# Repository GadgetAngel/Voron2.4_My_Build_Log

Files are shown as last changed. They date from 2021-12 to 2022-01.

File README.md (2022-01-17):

## This is a Build Log for my Voron 2.4 250 mm DIY 3D Printer called "QUEEN":

My Voron 2.4 3D Printer has a name "QUEEN".

This repository contains wiring diagrams, specification sheets, any documentation I use to complete my Voron 2.4 build. I also am including aesthetic designs for QUEEN's back panel and side panels.

# This repository uses LFS extension

```
I use Git for Windows with VScode to manage this repository.  I also use Git LFS extensions for all the files.

Install Git with LFS extensions: https://git-lfs.github.com/

To Download the whole repository do the following: select the "Clone or download button" and
click on "paste to clipboard" button so you can place the URL for the GitHub repository
to the clipboard. Now Open Git Bash.  Change the current working directory to the location
where you want the cloned directory.
Type git clone, and then paste the URL you copied earlier.
$ git clone https://github.com/GadgetAngel/Voron2.4_My_Build_Log.git
Press Enter to create your local clone.
Now open Window explorer to the location of local clone.
```

## This whole repository can be downloaded as one large zip file from my Google Drive at: (if downloading via LFS is giving you are hard time)

## xxxxxxxxxxxxxxxxxxxxxxxxxxxxxxxxxxxxxxxxxxxxx

## Mother board I plan on using:

I will be using the Octopus Pro V1.0 board as the mother board for my Voron 2.4 printer.
I will be powering my TMC5160 PRO stepper motor drivers with 48V DC.

## Planning Phase:

I am ~~still planning~~ done planning my Voron 2.4 build.

I have all my PIF parts and sourced all my parts via "sub-kits".  This will be explained later.

I wanted to post an Excel spreadsheet for sourcing all my "sub-kits" or individual items for my Voron 2.4 ~~, but I need to remove it from a bigger spreadsheet I have been using to keep track of a lot of different information.  After I get done with the electronics case wiring diagram, I will work on providing a~~ [Here is the Excel spreadsheet as a sourcing guide for my Voron 2.4](/QUEEN_Sourcing_BOM).

## MODS I plan for QUEEN:

### Fusion 360 CAD files and STEP files:

I have spent 3 months creating the 3D model of my QUEEN Voron 2.4 250 mm³ build.

I have used the CAD models from each MOD (listed below) and incorporated the respective MOD's CAD model into my QUEEN Fusion 360 model.  After working in Fusion 360 for the past 3 months I have become aware of a couple of things:

1.  When exporting sub-Assemblies from Fusion 360 in .STEP format the only sub-assemblies that get put into the STEP file are the sub-assemblies that are visible at the time the exported STEP file is created.  So when you use STEP files expect all the sub-assemblies to be visible when you first open up the STEP file.  You will have to turn off the options that you do not want to see after you upload the STEP file to Fusion 360 (or your CAD software).

2. If a MOD did not have a Fusion 360 CAD model, I used the .stl files from the MOD and used Fusion 360 to convert the .stl files into parametric bodies.

3.  If you upload .f3d sub-Assembly file and all sub-assembly options are turn on, then please just turn off the sub-assemblies you do not want to see. Sometimes, I exported the .STEP files at the same time I was creating the .f3d files, I might have left options turned on, so I could save the .STEP file.

4. I have noticed that if one uses the "save a copy as ..." option that parts will lose their position (x,y,z).  So to create the sub-assemblies I did a "copy" to the clip board and then placed the clip board contents into a new file and saved that file.

GadgetAngel's Voron 2.4 Fusion 360 CAD model (.f3d) and (.STEP) files:

The full model for QUEEN has a fusion 360 (.f3d) file and STEP file.  The STEP file for the full model has been integrated by myself from all the sub-assemblies STEP files. This way I could check the sub-assembly files to ensure that they were created correctly.

1.  [QUEEN's Voron 2.4 Fusion 360 model and STEP version](./CAD/QUEEN_Voron_2.4_Build_ZIP_files)

2.  [QUEEN's Voron 2.4 Fusion 360 subAssembly model (.f3d) and .STEP versions for the Electronics from the Bottom Electronics Case](./CAD/Electronics_forBottom_Electronic_Case/ZIP_files)

3.  [QUEEN's Voron 2.4 Fusion 360 subAssembly model (.f3d) and .STEP versions for Electronics from the LitterBox Case](./CAD/Electronics_forLitterBox_Case/ZIP_files)

4.  [QUEEN's Voron 2.4 Fusion 360 subAssembly model (.f3d) and .STEP versions for the LEDs](./CAD/LEDs/ZIP_files)

5.  [QUEEN's Voron 2.4 Fusion 360 subAssembly model (.f3d) and .STEP versions for all Panels & Clips](./CAD/Panel_Mounting/QUEENv98_SubAssmbly_Panel&Clips_ZIP_files)

6.  [QUEEN's Voron 2.4 Fusion 360 subAssembly model (.f3d) and .STEP versions for different panels, see this directory for additional sub-assemblies](./CAD/Panel_Mounting)

7. [QUEEN's Voron 2.4 Fusion 360 subAssembly model (.f3d) and .STEP versions for all Skirts](./CAD/Skirts/QUEENv98_SubAssmbly_ALL_Skirts_ZIP_files)

8. [QUEEN's Voron 2.4 Fusion 360 subAssembly model (.f3d) and .STEP versions for different Skirts (i.e., Front Skirt, Left-Side Skirt, etc.), see this directory for additional sub-assemblies](./CAD/Skirts)

9. [QUEEN's Voron 2.4 Fusion 360 subAssembly model (.f3d) and .STEP versions for all the mods located under the Heated Bed & a Filament Runout Sensor](./CAD/Under_Heated_Bed/ZIP_files)

10. [QUEEN's Voron 2.4 Fusion 360 subAssembly model (.f3d) and .STEP versions for my Z Driver Tensioner Mod](./CAD/Z_Drive/ZIP_files)

11. [QUEEN's Voron 2.4 Fusion 360 subAssembly model (.f3d) and .STEP versions for the Exhaust Filter](./CAD/Exhaust_Filter/ZIP_files)

12.  [QUEEN's Voron 2.4 Fusion 360 subAssembly model (.f3d) and .STEP versions for the Frame](./CAD/Frame/ZIP_files)

13. [QUEEN's Voron 2.4 Fusion 360 subAssembly model (.f3d) and .STEP versions for the Gantry](./CAD/Gantry/ZIP_files)

14. [QUEEN's Voron 2.4 Fusion 360 subAssembly model (.f3d) and .STEP versions for the Litter Box Mod and its sub-assemblies, see this directory for additional sub-assemblies](./CAD/Litter_Box_CAD)

15. [QUEEN's Voron 2.4 Fusion 360 subAssembly model (.f3d) and .STEP versions for the Z-Endstop called the "SexBolt Z-Endstop"](./CAD/Z_Endstop/ZIP_files)

16. [QUEEN's Voron 24 Fusion 360 subAssembly model (.f3d) and .STEP version for the BTT piTFT50 V2.0 articulating arm with display mount](./CAD/Skirts/Front/Middle/ZIP_files)

---

### ".STL List" of files needed for each MOD:

I will be publishing a folder of .stl files for all the printed parts I am using for my QUEEN build, including the ones from my PIF parts ~~(coming soon)~~.

My intent is to list the files needed in each Sub-Assembly and indicate which ".stl files" need to be replaced or exchanged for a Modded ".stl" file.  I think an EXCEL spreadsheet would help with this task and can be found [here](/The_.STL_Files/Excel_Spreadsheet_.stl_files).

The ".STL" files for my QUEEN Voron 2.4 build can be found [here](./The_.STL_Files/Copy_of_.STLs_forQUEEN_As_Built_will-not-be-updated)

---

### Voron 2.4 MODS I plan on using for my Build (250 mm³ Build):

Tool head PCB board (MOD) I am using:

1. [Hartk1213's "Voron Afterburner Toolhead Board v3.rabbit (also known as ERCF PCB board)"](https://github.com/VoronDesign/Voron-Hardware/tree/master/Afterburner_Toolhead_PCB).

    * [Buy Hartk1213's ERCF PCB board at deepfriedhero.in website](https://deepfriedhero.in/products/voron-afterburner-toolhead-board-v3-rabbit?_pos=1&_psq=v3.&_ss=e&_v=1.0)

    * [Wiring Diagram for "Voron Afterburner Toolhead Board v3.rabbit"](https://github.com/VoronDesign/Voron-Hardware/blob/master/Afterburner_Toolhead_PCB/Images/Wiring/ERCF-Toolhead%20SKR%201_4%20wiring.png)

    * Also see my [wiring harness diagram!](https://github.com/GadgetAngel/Voron2.4_My_Build_Log/blob/main/Wiring_Harness_Diagram/Voron_2.4_Tool_Head_PCB__Wiring_Harness.jpg)

---

Other MODS I am using for my QUEEN build (Z belts 9 mm; XY belts 6 mm):

1. [Arkeet's "MGN12 Mod"](https://github.com/VoronDesign/VoronUsers/tree/master/printer_mods/arkeet/mgn12);

2. [Hartk1213's "PINS Mod"](https://github.com/hartk1213/MISC/tree/main/Voron%20Mods/Voron%202/2.4/Voron2.4_Pins_Mod);

3. [Ramalama2's "Misumi_RBPB5 Mod"](https://github.com/Ramalama2/Voron-2-Mods/tree/main/Misumi_RBPB5);
[Note: this replaces the GE5C Mod](https://github.com/hartk1213/MISC/tree/main/Voron%20Mods/Voron%202/2.4/Voron2.4_GE5C);

4. [0ndsk4's "Nevermore Micro Filter Mod"](https://github.com/nevermore3d/Nevermore_Micro);

5.  I combined two user mods into one mod for the "Z Drive Motor Tensioner Mod":

    * Z Motor A/B Unit combined from [Edwardyeeks' "V2.4_z_drive_motor_tensioner_mod"](https://github.com/VoronDesign/VoronUsers/tree/master/printer_mods/edwardyeeks/V2.4_z_drive_motor_tensioner_mod); with my modification for the front Skirts for switches and Hour counter;

    * Z Motor A/B Motor Unit combined from [Spaghetti-Bolognese's "Z Driver System Mods"](https://github.com/VoronDesign/VoronUsers/tree/master/printer_mods/Spaghetti-Bolognese/Z_drive_motor_mount);

6. [Jlas1's "Klicky Probe Mod"](https://github.com/jlas1/Klicky-Probe) and information about the Klicky Probe mod from [Ramalama2's "KlickyShare GitHub repo"](https://github.com/Ramalama2/Voron-2-Mods/tree/main/KlickyShare); I also used the following "user mods" for the "Klicky Probe Mod":

    *   ~~[bluedragonx's "BlueDragonX's Klicky Mods" ](using built-in Klicky Probe to X-Axis Carriage Frame): https://github.com/jlas1/Klicky-Probe/tree/main/Printers/Voron/v1.8_v2.4_Legacy_Trident/Usermods/bluedragonx;~~

     Bluedragonx's user mod changes the X-Axis Carriage Frame pieces to allow for a built-in Klicky Probe. I decided to use the regular Klicky Probe mode and a combination of the following two user mods for the Klicky Probe body (this way the Klicky Probe is **not** built into the X-Axis Carriage) and I can decide to use the Euclid Probe, if I so desire [See item #47](#47-derpimus-euclide_probes-omronrotatedxraildock_v2):

    *   [StefanRaatz's Klicky Mods](https://github.com/jlas1/Klicky-Probe/tree/main/Printers/Voron/v1.8_v2.4_Legacy_Trident/Usermods/StefanRaatz); This is a modified Klicky probe with two holes so that you can feed through the uninsulated part of the cable a little more. Gave me better contact.

    *   [Oc_geek's More Robust Klicky Probe Mod](https://github.com/jlas1/Klicky-Probe/tree/main/Printers/Voron/v1.8_v2.4_Legacy_Trident/Usermods/oc_geek); Beefier column and revised holes for zip tie (was def too small); reduced height 1 mm (was excess) Chambered bottom in all direction (also sides) on the probe carriage Microswitch body exposed by a tiny bit.

7. [Whoppingpochard's "Ti Backers Mod"](https://github.com/tanaes/whopping_Voron_mods/tree/main/extrusion_backers); Y backers 30 mm from front; X backer 35 mm from the Y axis drag chain;

8. [Ramalama2's "Front_Idlers mod" ](https://github.com/Ramalama2/Voron-2-Mods/tree/main/Front_Idlers); - these are replacement for Phalanx's "Other-V2-Idlers" mod;

    * Here is the information on Phalanx's "Other-V2-Idlers mod" if you are interested.  [Phalanx's "Other-V2-Idlers mod"](https://github.com/VoronDesign/VoronUsers/tree/a425971f2986578e2e5c10e638f59d02172687c1/printer_mods/Phalanx/Other-V2-Idlers);

~~9. [Badnoob's "AB-BN30 Afterburner mod"](https://github.com/VoronDesign/VoronUsers/blob/master/printer_mods/Badnoob/AB-BN/Readme.md);~~ I will be using the Stealthburner Mod instead. [Please see item #48](#48-voron-design-teams-stealthburner-mod)

####     10.	[Hartk1213's "Sexbolt Z-Endstop Mod"](https://github.com/hartk1213/MISC/tree/main/Voron%20Mods/Voron%202/2.4/Voron2.4_SexBolt_ZEndstop);

11.	Cover for Toolhead, I created my own ([in this repository](https://github.com/GadgetAngel/Voron2.4_My_Build_Log/blob/main/The_.STL_Files/Copy_of_.STLs_forQUEEN_As_Built_will-not-be-updated/Gantry/X_Axis/X_Carriage/Direct_Fee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)) - from [Hartk1213's "ERCF covers for the LGX extruder"](https://github.com/VoronDesign/Voron-Hardware/tree/master/Afterburner_Toolhead_PCB/STLs/LGX); I cut the front of the LGX cover for ERCF cover for Stealthburner. See also [Th3fallen's website for the LGX_PCB_Mount_Heatset.stl file](https://github.com/th3fallen/Voron-Hardware/tree/feature/add-heatset-lgx-pcb-mount/Afterburner_Toolhead_PCB/STLs/LGX);

12.	[Whoppingpochard's "Z_Drive_Belt_Exit_Covers Mod"](https://github.com/tanaes/whopping_Voron_mods/tree/main/Z_belt_cable_cover);

13.	[Edwardyeeks' "Decontaminator_Purge_Bucket_&_Nozzle_Scrubber Mod"](https://github.com/VoronDesign/VoronUsers/tree/master/printer_mods/edwardyeeks/Decontaminator_Purge_Bucket_%26_Nozzle_Scrubber);

14.	[Hernsl's "Bottom_panel_mag_clip Mod"](https://github.com/VoronDesign/VoronUsers/tree/master/printer_mods/hernsl/bottom_panel_mag_clip);

15.	[Wile-e1's "Deck_Panel_Support_Clips Mod"](https://github.com/VoronDesign/VoronUsers/tree/master/printer_mods/wile-e1/Deck_Panel_Support_Clips);

16.	[Tayto-chip's "Skirt_switch_mod"](https://github.com/VoronDesign/VoronUsers/tree/master/printer_mods/tayto-chip/skirt_switch_mod) - with my modifications;

17.	[Leandromarceddu's "PowerSkirt Mod"](https://github.com/VoronDesign/VoronUsers/tree/master/printer_mods/leandromarceddu/PowerSkirt) - with my Modifications;

18.	[StvPtrsn's "Side_Fan_Support_No_Tape Mod"](https://github.com/VoronDesign/VoronUsers/tree/master/printer_mods/StvPtrsn/Side_Fan_Support_No_Tape);

19.	[MarcPot's "Skirt_Mod_250 Mod"](https://github.com/VoronDesign/VoronUsers/tree/master/printer_mods/MarcPot/Skirt_Mods); - with my modification so that you can use this with the magnetic bottom panel;

20. My BTT-PITFT5-Mount Mod come from the following sources:

    * [Alanho's "BTT_PITFT50_v2_Mount Mod"](https://github.com/VoronDesign/VoronUsers/tree/master/printer_mods/alanho/BTT_PITFT50_v2_Mount);

    * [Smaseface's "BTT-PITFT5-Mount mod"](https://github.com/smaseface/BTT-PITFT5-Mount-for-Voron-v2.4);

    * [Revnull's "Articulating arm" from his "rpi_7in_display_mount mod"](https://github.com/VoronDesign/VoronUsers/tree/master/printer_mods/revnull/rpi_7in_display_mount);

    * [driftology's "Fysetc Paneldue 7i V3 Voron 2 Adapter on Thingiverse.com"](https://www.thingiverse.com/thing:4571677);

21.	[Randell's "Microswitch_Endstop POD"](https://github.com/VoronDesign/VoronUsers/tree/master/printer_mods/randell/Microswitch_Endstop);

22. [Ramalama2's "Misumi_Cable_Clip mod"](https://github.com/Ramalama2/Voron-2-Mods/tree/main/Misumi_Cable_Clip);

23. [Ramalama2's "AB_Plug_Microfit mod"](https://github.com/Ramalama2/Voron-2-Mods/tree/main/AB_Plug_Microfit); or [AB_Plug_JST-XHmod](https://github.com/Ramalama2/Voron-2-Mods/tree/main/AB_Plug_JST-XH); or you could also use the Voron Design Team's ["Tie-down the AB motors cables to the Z-Beam Mod"](https://github.com/VoronDesign/Voron-2/blob/Voron2.2/STLs/VORON2.2/Gantry/%5Ba%5D_cable_anchor_x4_rev1.stl);

####       24.  [Ramalama2's "Panel_Clips"; I will use the midspan clips for sides and top](https://github.com/Ramalama2/Voron-2-Mods/tree/main/Panel_Clips); - (use 6 mm version - 3 mm panel and 3 mm of foam tape);

25. [Richardjm's "ADXL345 Mount Mod"](https://github.com/richardjm/VoronUsers/tree/richardjm/adxl-chain/printer_mods/richardjm/adxl-chain); I used information from [Padok's ADXL345 Mount](https://github.com/VoronDesign/VoronUsers/tree/master/printer_mods/padok/chain_anchor-ADXL345_mount);

26. [Eddie's "LED_Bar_Clip mod"](https://github.com/VoronDesign/VoronUsers/tree/master/printer_mods/eddie/LED_Bar_Clip);

27. [Hartk1213's "AB Spinner (Voron2.4_Spinner) mod"](https://github.com/hartk1213/MISC/tree/main/Voron%20Mods/Voron%202/2.4/Voron2.4_Spinner); or [Rubber Ducky Spinner Mod](https://discord.com/channels/460117602945990666/828406858271162378/875463215721644032)

28. [42bios' "corner_panel_clip_cable mod"](https://github.com/VoronDesign/VoronUsers/tree/master/printer_mods/42bios/corner_panel_clip_cable); Also my own modification for these clips so I can use them to mount the Mikro10 Illumination Edge Bracket on the side panels.

29. [OV1A's "WAGO+221+DIN+rail+holder mod" from Thiniverse.com](https://www.thingiverse.com/thing:4972435); Used to mount the WAGO nuts on the DIN rails.

30. [The0bone's "Voron 2.4 China Chain Guide mod" on Prusaprinters.org](https://www.prusaprinters.org/prints/69683-voron-24-china-chain-guide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);

31. For handling the thermal expansion on the Build Plate for QUEEN, I added the Mandala Rose Works's ["Matched Height Kinematic Kit"](https://www.mandalaroseworks.com/shop/voron/matched-height-kinematic-kit) along with ["Voron 250 Standard Bed"](https://www.mandalaroseworks.com/shop/voron/voron-250-standard-bed),

    The following will be needed if you add the kinematic kit to your Voron 2.4 Build:
    *  [Modified Purge Bucket](https://github.com/GadgetAngel/Voron2.4_My_Build_Log/tree/main/The_.STL_Files/GA_modded_STLs/Decontaminator_Purge_Bucket_%26_Nozzle_Scrubber_MOD);
    *  [buy a longer sexbolt for](https://www.amazon.com/gp/product/B07GSQZWNP) [Item #10](#10hartk1213s-sexbolt-z-endstop-mod) and
    *  buy some [Openbuild's Angled brackets](https://deepfriedhero.in/products/openbuilds-angle-corner-connector?_pos=2&_sid=c4c7e2ca4&_ss=r), or you could just use blind joints;

32. [GadgetAngel's "Litter Box mod"](https://github.com/GadgetAngel/Voron2.4_My_Build_Log/tree/main/Electronics_Case_Wiring_Diagram/Litter_Box_Mod);

33. I also used all [Trident DIN clips](https://github.com/VoronDesign/Voron-Trident/tree/main/STLs/ElectronicsBay) for mounting electronics and I used [Trident 3D Printed Parts on the MGN12 Mod](https://github.com/VoronDesign/Voron-Trident/tree/main/STLs/Gantry/X_Axis/X_Carriage). **Thank you, Voron Design Team for all your hard work!**

34. [Nemgrea & Geoffreyyoung's "LGX Extruder Mod to replace the Clockwork extruder"](https://github.com/VoronDesign/VoronUsers/tree/master/printer_mods/geoffreyyoung/lgx);

35. [LoCoCNC's "Wire_grommets"](https://github.com/VoronDesign/VoronUsers/tree/master/printer_mods/LoCoCNC/wire_grommets); modified for Kinematic Bed;

36. [Danowar's "Humidity_Sensor_Bracket"](https://github.com/VoronDesign/VoronUsers/tree/master/legacy_printers/printer_mods/Danowar/Humidity_Sensor_Bracket);

37. [Mikro10 Illumination Edge Bracket for the Side panels](https://www.wired4signsusa.com/products/edge-lit-led-extrusion-for-1-4-acrylic-mikro10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); I modified [42bios' "corner_panel_clip_cable mod"](https://github.com/VoronDesign/VoronUsers/tree/master/printer_mods/42bios/corner_panel_clip_cable) so I could mount the Mikro10 illumination edge bracket to light the side panels.

38. [Boingomw's "Wago_mount mod"](https://github.com/VoronDesign/VoronUsers/tree/master/printer_mods/Boingomw/Wago_mount) used for Wago mount near the Build Plate;

39. [GSL12's "wago_221_mount mod"](https://github.com/VoronDesign/VoronUsers/tree/master/legacy_printers/printer_mods/GSL12/wago_221_mount); Used these to place Wago nuts around the whole Voron 2.4 printer mounted to the extrusions.

40. [Jeoje's "Molex_MLX_Microfit_Bed_Connector_Mount Mod"](https://github.com/VoronDesign/VoronUsers/tree/master/printer_mods/jeoje/Molex_MLX_Microfit_Bed_Connector_Mount);

41. [Richardjm's "Backplate blanking plate mod"](https://github.com/VoronDesign/VoronUsers/tree/master/printer_mods/richardjm/back-plate);

42. [Jeoje's "Z_Chain_Guide_Thermistor_Mount mod"](https://github.com/VoronDesign/VoronUsers/tree/master/printer_mods/jeoje/Z_Chain_Guide_Thermistor_Mount);

43. [BladeScraper-Designs' "Horizontal-Spool-Holder Mod"](https://github.com/VoronDesign/VoronUsers/tree/master/printer_mods/BladeScraper-Designs/Horizontal-Spool-Holder);

44. [Empusas' "BTT_Filament_Motion_Sensor_Mount Mod"](https://github.com/VoronDesign/VoronUsers/tree/master/printer_mods/Empusas/BTT_Filament_Motion_Sensor_Mount);

45. [Ellis' "Bed_Fans Mod"](https://github.com/VoronDesign/VoronUsers/tree/master/printer_mods/Ellis/Bed_Fans);

46. [Ramalama2's "Misumi_Led_Corners"](https://github.com/Ramalama2/Voron-2-Mods/tree/main/Misumi_Led_Corners);

#####     47. [Derpimus' Euclide_Probe's "OmronRotatedXRailDock_v2"](https://discord.com/channels/460117602945990666/916406093339566120/923047248051462226);

#####     48. [Voron Design Team's "Stealthburner Mod"](https://github.com/VoronDesign/Voron-Afterburner/tree/sb-beta/STLs);

49. [Voron Design Team's "Z Rail end stops"](https://github.com/VoronDesign/Voron-2/blob/Voron2.2/STLs/VORON2.2/Gantry/%5Ba%5D_z_rail_stop_x4_rev1.stl);

50. [AlexanderT-Moss's 270-Clamping-Hinges for the front doors](https://github.com/VoronDesign/VoronUsers/tree/master/printer_mods/AlexanderT-Moss/270-Clamping-Hinges) [instead of Item #24's Front door clips](#24--ramalama2s-panel_clips-i-will-use-the-midspan-clips-for-sides-and-top---use-6mm-version---3mm-panel-and-3mm-of-foam-tape);

51. [AlchemyEngine's Skirt-Microfit-Inserts](https://github.com/alchemyEngine/EnragedRabbitProject/tree/main/usermods/Skirt-Microfit-Inserts) - I modified it. So I could [mount a Reset button for the BTT V1.2 Relays](https://github.com/GadgetAngel/Voron2.4_My_Build_Log/blob/main/The_.STL_Files/Copy_of_.STLs_forQUEEN_As_Built_will-not-be-updated/LitterBox_Mod/Electronics/%5Ba%5D_R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) shown on my AC Wiring Diagram;

52. [V6cl's Lift Handles](https://github.com/v6cl/My-Voron2.4-Customs/tree/main/LiftHandle) - I modified the [Lift Handles](https://github.com/GadgetAngel/Voron2.4_My_Build_Log/tree/main/The_.STL_Files/Copy_of_.STLs_forQUEEN_As_Built_will-not-be-updated/Panel_Mounting/LiftHandles_11mm), so they will fit my side panels which have edge lighting.  Instead of 7 mm clearance I will need 11 mm clearance.

53. [V6cl's Panel_Locker](https://github.com/v6cl/My-Voron2.4-Customs/tree/main/Panel_Locker) as the front door handles.

If you are looking for 3D CAD models for the different Voron Build plates you can find them at https://github.com/lecktor/Voron-V2.4

I created a 3D CAD model for the Mandala Rose Works's MIC6 Build plate for the 250 mm build. You can find it at https://github.com/GadgetAngel/Voron2.4_My_Build_Log/tree/main/CAD/Under_Heated_Bed.

## How I Calculated the Power Requirements for my Voron 2.4 Build:

I know a lot of you already know the answer but for the rest of us that are still learning about bipolar stepper motors and stepper drivers I will describe the process I used.  I never realized that the motors I own are **bipolar-series motors**.

To me when things are connected in series the wires are daisy-chained together (positive lead1, negative lead1 is connected to positive lead2, negative lead2).

When things are wired in parallel then the positive leads are connected together and the negative leads are connected together.

So I thought the 3D printer motors where connected together in parallel on the 3D printer, which they are. If you look at the **system in a "macro" view** not a "micro" view.

My problem was not understanding the term "series" and "parallel" when it applies to the internal wiring of the 4-wire bipolar motor (a "micro" view).

I had to look at an 8-wire bipolar motor before I actually got it through my thick head.

Maybe this will help others:

[Drawing of 8 wire bipolar-parallel motor](https://www.google.com/imgres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)

[Drawing of 8 wire bipolar-series motor](https://www.google.com/imgres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)

So ALL my motors are 4-wire bipolar-series motors!

 To Determine the amount of Power Required for your Voron 2.4 build:

 Fact: During a Z Hope move 6 motors will be active at a time.

 Fact: Extruder (E) Motor LDO-42STH20-1004ASH:
		Rated Peak current: 1.0A/ Phase

 Fact: Z motors and AB motors are LD0-42STH40-2004MAH
		Rated Peak current: 2.0A / Phase

 Rule of Thumb (https://robotics.stackexchange.com/a/16333/31219):

 1. Power_supply_current = number_of_motors * 1/3 * motor_peak_current for "bipolar-series motors" (All LDO motors are bipolar-Series Motors!)

 2. Power_supply_current = number_of_motors * 2/3 * motor_peak_current for "bipolar-parallel motors"

 Since ALL LDO motors I own are bipolar-Series Motors we will use Rule of Thumb #1 ONLY!

 Power_ supply_current = (5 * 1/3 * 2.0 Amps) + (1 * 1/3 * 1.0A) = 3.333 + 0.333 = 3.6667 or 4 Amps.

 So for **my bipolar-series motors** I want to know many Watts of power is 4 Amps at 48 VDC?

 Answer: Watts = Volts * Amps

 So, 48VDC * 4 Amp = 192 Watts or 200 Watts PSU (if the PSU supplies the full power without an aluminum plate for heat dissipation [PSU's Derating Curve]).

Options for powering my Voron 2.4 printer at 48 VDC, and 24 VDC (running all HT motors from LDO at 48VDC) with the following:

See UHP-200 Spec Data sheet : https://www.meanwellusa.com/upload/pdf/UHP-200(R)/UHP-200-spec.pdf

See UHP-350 Spec Data sheet : https://www.meanwellusa.com/upload/pdf/UHP-350(R)/UHP-350-spec.pdf

See UHP-500 Spec Data sheet : https://www.meanwellusa.com/upload/pdf/UHP-500(R)/UHP-500-spec.pdf

If you are having a hard time finding UHP-xxx series of power supplies, there are two names for these UHP supplies.  One name is UHP-350-24, UHP-350-48 and so on. While the other name is UHP-350R-24, UHP-350R-48 and so on.  The extra "R" in the model number just indicates that you have the option of wiring 2 power supplies in parallel.  The "R" version will work if you can not find the regular version to buy.

---

1. 48V PSU UHP-200-48 (AC to DC PSU)[(4.2A*0.8)= 3.36 Amps; I need 4 Amps! [without an aluminum plate, so 80%]] : https://www.digikey.com/en/products/detail/mean-well-usa-inc/UHP-200-48/7707242

2. 24V PSU UHP-200-24 (AC to DC PSU)[(8.4A*0.8)= 6.72 Amps ; I want at least 9 Amps! [without an aluminum plate, so 80%]]: https://www.digikey.com/en/products/detail/mean-well-usa-inc/UHP-200-24/7707239

---

3. 48V PSU UHP-350R-48 (AC to DC PSU)[(7.3A*0.70)= 5.32 Amps; I need 4 Amps [without an aluminum plate, so 70%]] : https://www.digikey.com/en/products/detail/mean-well-usa-inc/UHP-350-48/7707258; https://www.newark.com/mean-well/uhp-350r-48/power-supply-ac-dc-48v-7-3a/dp/01AH8032?ost=uhp-350r-48

4. 24 PSU UHP-350R-24 [(14.6A*0.70)= 10.22 Amps; I want at least 9 Amps [without an aluminum plate, so 70%]]: https://www.digikey.com/en/products/detail/mean-well-usa-inc/UHP-350-24/7707254;
https://www.newark.com/mean-well/uhp-350r-24/power-supply-ac-dc-24v-14-6a/dp/01AH8029?ost=uhp-350r-24

---

5. 48V PSU UHP-500-48 (AC to DC PSU)[(10.45*0.7)= 7.315 Amps; I need 4 Amps [without an aluminum plate, so 70%]] : https://www.digikey.com/en/products/detail/mean-well-usa-inc/UHP-500-48/8324039;
https://www.newark.com/mean-well/uhp-500-48/power-supply-ac-dc-48v-10-45a/dp/01AH8038?ost=uhp-500-48

6. 24V PSU UHP-500-24 (AC to DC PSU)[(20.9*0.7) = 14.63 Amps; I want at least 9 Amps [without an aluminum plate, so 70%]]: https://www.digikey.com/en/products/detail/mean-well-usa-inc/UHP-500-24/8324036; https://www.newark.com/mean-well/uhp-500-24/power-supply-ac-dc-24v-20-9a/dp/01AH8036?ost=uhp-500-24

---

So I could use option 3 & 4 **OR** 5 & 6.

Since I plan on LEDs; running a Raspberry Pi 4B with a solid state disk drive (via USB 3.1 interface instead of using a Micro-SD card); and a camera, I want to have enough power to add extras to the Voron Build.

I opted to buy the following:

1.  UHP-500-48 for my 48VDC supply
2.  UHP-500-24 for my 24VDC supply
3.  RS-25-5 for my 5VDC supply
4.   ~~UHP-200-12 for my 12VDC supply~~ Since I switched my LEDs from 12VDC and 24VDC so that all LEDs will be NeoPixels, I need another 5VDC PSU instead of a 12V PSU.  So I decided to by a combo PSU that will supply 5VDC and 12VDC. I purchased a [Meanwell RD-50A](https://github.com/GadgetAngel/Voron2.4_My_Build_Log/blob/main/Resources/MeanWell%20RD-50A%20specs.PDF)

I will use the Octopus Pro to power the stepper motor drivers, heater cartridge, temperature sensors, limit switches, and generate signals on PINs to control stuff, but I do not plan on powering stuff off the Octopus Pro board that is considered optional equipment like LEDs, an endoscope or cameras.  Since my Raspberry Pi (running Klipper) is the brains of this setup, I will be using a solid state drive to act as the disk drive for the Raspberry Pi.  This adds additional current draw and the Raspberry Pi will have its own 5V PSU.

All my LEDs are ~~12VDC or 24VDC~~ NeoPixels which are 5VDC. So that is why I am running a second separate 5VDC PSU and added additional current capability to my 24VDC supply.

I plan on running all TMC5160 (HV) PRO stepper motor drivers for all my motors on QUEEN.
I know this is an overkill but if I want the power it will be there, and I do not want to redo wiring at a later date.

~~Likewise, I am hoping to fit all of my electronics into the electronics case for a 250 mm build.~~ Edited: There is not enough room for all the PSU and all the electronics therefore I developed my own "Litter Box" Mod, so I can keep the AC Power in the bottom electronic's case and use my "Litter Box" for the DC electronic components.

[Click here to get explanation about the "Litter Box" Mod](https://github.com/GadgetAngel/Voron2.4_My_Build_Log/tree/main/Electronics_Case_Wiring_Diagram/Litter_Box_Mod).

1/5/2022: Click [here](https://github.com/GadgetAngel/Voron2.4_My_Build_Log/tree/main/Electronics_Case_Wiring_Diagram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) to see further information about the "Voron 2.4 AC wiring diagram".

Click here see the JPG file for the ["Voron 2.4 AC Electrical Wiring Diagram"](https://github.com/GadgetAngel/Voron2.4_My_Build_Log/tree/main/Electronics_Case_Wiring_Diagram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)

To download the PDF just click on the filename ["Voron_2.4_Electronics_Case_Wiring_Diagram_AC_wiring.pdf"](images/Voron_2.4_Electronics_Case_Wiring_Diagram_AC_wiring.pdf) and hit the download button.

## How did I go about calculating the size of the UPS Battery Backup Units I needed for the QUEEN Build and the Voron 2.4-LDO Build

First off, if you have not heard I bought the Voron 2.4 300 mm³ LDO kit.  I need to build a "close to spec" Voron 2.4 printer so that I can build my dream printer "QUEEN".  This way I will have a work horse printer that I can use to further develop my modifications I am making to the QUEEN build.

Back to the issue at hand.  How did I determine the amount of VAC I would need for each of my Voron 2.4 builds?  Once you decide on the power supply units (PSUs) you will be using for your build, get hold of the data sheets for each of the PSU and look at the specification called "INPUT" "AC Current (typ.)" there should be an amount of amps listed for either 115VAC or 230VAC.  For the USA and corresponding countries that use 120VAC (60Hz) or you will see on the spec sheet of the PSU a listing for "115VAC".  While Europe uses 230VAC (50Hz), you will see on the spec sheet of the PSU a listing for "230VAC".  Take the "INPUT AC Current (typ.)" values for your type of power distribution system and add them all together to get a total "INPUT AC Current (typ.)" value. So for sake of an example, I am in the USA, so I added all my "INPUT AC Current (typ.)" values together for my 4 PSU and got a total "INPUT AC Current (typ.)" = 11.7 amps for the QUEEN build.

Now I was looking at the [APC UPS 1500VA UPS Battery Backup and Surge Protector Unit from Amazon](https://www.amazon.com/gp/product/B06VY6FXMM). It says in the title that is has 1500VA. So I take that number and divide 115VAC into it to give me the total INPUT AC Current (typ) that this UPS Battery Backup unit can handle.  So 1500/115 = 13.0434782 Amps maximum.  I only need 11.7 amps. So take 11.7/13.0434782 to see what % of the total I will be using = 0.89699 or 89.699%. So I have 100%-89.699% of overhead left unused which is equal to 10.30% left unused.  As long as I have at least 10% unused overhead available, I will purchase the unit.

Now let us look at the Voron 2.4 LDO kit. When I add up all the "INPUT AC Current (typ.)" values for that build I get a total of 4 Amps.  I have an extra APC UPS unit here at my home that is called [APC UPS 850VA UPS Battery Backup & Surge Protector](https://www.amazon.com/gp/product/B01HDC21FE). So I take 850/115 = 7.3913 Amps maximum.  I am only using 4 Amps. What is my left unused overhead value? 1-(4/7)*100=42.86%. I feel better with an overhead that large.  I personally would not buy a UPS unit that did not give me at least a 10% unused overhead value.

## How to calculate the Amps required for the BIG RED mushroom button

Added on 1/11/2022:

To calculate the total "INPUT AC Current Draw" from your Voron 2.4 build, look at each of the PSUs you have included in your Voron 2.4.  On the data sheet for the PSUs you will see a specification labeled "INPUT" "AC Current (typ.)" there should be an amount of amps listed for either 115VAC or 230VAC. Take the "INPUT AC Current (typ.)" values for your type of power distribution system and add them all together to get a total "INPUT AC Current (typ.)" value.

So for example, I am in the USA, so I added all my "INPUT AC Current (typ.)" values together for the 115VAC option and my 4 PSUs and draw a total "INPUT AC Current (typ.)" value of 11.7 Amps for the QUEEN build. For the Voron_LDO build by total "INPUT AC Current (typ.)" value is 4 Amps.

I purchased this [BIG RED Mushroom Emergency Button](https://www.amazon.com/gp/product/B07RJMVPJ4) which is rated up to 10 Amps. So, for the Voron_LDO build this [BIG RED Mushroom Emergency Button](https://www.amazon.com/gp/product/B07RJMVPJ4) will work without modification.  I can run both the AC "LINE" and the AC "NEUTRAL" wires from the wall outlet into the "BIG RED" mushroom button and use the two NC contacts to switch those lines (one contact per wire).

But for the QUEEN Build the total "INPUT AC Current (typ.)" value is 11.7 Amps, which is above the rated 10 Amps for this [BIG RED Mushroom Emergency Button](https://www.amazon.com/gp/product/B07RJMVPJ4).  The problem is I could not find a BIG RED Mushroom Emergency Button that is rated for 20 Amps on Amazon.  So this is what I have opted to do.  In the USA, we really do not need to switch the AC "Neutral" wire but switching the AC "Line" wire is what is really needed.  Since this [BIG RED Mushroom Emergency Button](https://www.amazon.com/gp/product/B07RJMVPJ4) has TWO normally closed (NC) contacts and each contact is rated for 10 Amps, I can just run the AC "Line" wire into the two NC contacts in parallel. Think of the BIG RED Mushroom button as a DPST switch.  By wiring the contacts up in parallel then each contact will handle 10 Amps and now my BIG RED Mushroom Button can handle 20 Amps on the AC "Line" wire. On the output of the NC contacts the two AC "Line" wires are brought back together for a single output feed.

~~So now I need to change my "AC wiring diagram" to reflect this change in the BIG RED button for the QUEEN Build.~~
I have updated the ["AC wiring diagram"](https://github.com/GadgetAngel/Voron2.4_My_Build_Log/blob/main/images/Voron_2.4_Electronics_Case_Wiring_Diagram_AC_wiring.pdf) to reflect the changes to the BIG RED mushroom Emergency Button.  

I also modified the [Skirt-Microfit-Inserts Mod from Ette's ERCF project](/The_.STL_Files/GA_modded_STLs/Skirt/Front/A/%5Ba%5D_Button_mount%20Z-tensioner_Mod_Front_OR_Rear_Hour_Counter_Skirt_A_300_x2.stl) so that I would have a place to mount QUEEN's "Reset Printer Only"
buttons.  The other four switches will control four Neopixel LED Strings, and they will be on the "DC wiring diagram". I also need to print the 300 mm front skirt version so that I have a place to mount this "Skirt_Insert" called "\[a\]_Button_mount Z-tensioner_Mod_Front_OR_Rear_Hour_Counter_Skirt_A_300.stl" and "\[a\]_Button_mount_Front_OR_Rear_Rocker-switches_Skirt_B_300.stl".

To learn more about parallel circuits see [UNDERSTANDING & CALCULATING PARALLEL CIRCUITS - EXPLANATION](https://www.swtc.edu/Ag_Power/electrical/lecture/parallel_circuits.htm)

Here is a diagram on how to wire two NC contacts up in parallel:

ParallelDiagram

## The PDF file of the "Color PIN Diagram" for the Octopus Pro V1.0:

You can view the PDF in your browser by clicking on the filename ["BIGTREETECH-Octopus-Pro-V1.0-Color-PIN-V3.0.pdf"](https://github.com/GadgetAngel/BTT_Octopus_Color_PIN_Diagram/blob/main/BTT_Octopus_Pro_V1.0_Color_PIN_Diagram/BIGTREETECH-Octopus-Pro-V1.0-Color-PIN-V3.0.pdf) and then hit the download button.

You can view an even higher resolution image (give it a minute or two to load, it takes longer due to the higher resolution) when you view the PDF in your browser by clicking on the filename ["BIGTREETECH-Octopus-Pro-V1.0-Color-PIN-V3.0-400ppi.pdf"](https://github.com/GadgetAngel/BTT_Octopus_Color_PIN_Diagram/blob/main/BTT_Octopus_Pro_V1.0_Color_PIN_Diagram/BIGTREETECH-Octopus-Pro-V1.0-Color-PIN-V3.0-400ppi.pdf) and then hit the download button.

## A Picture of the "Color PIN Diagram" for the Octopus Pro V1.0:

You can download the JPG file for this "Color PIN Diagram" by clicking on the filename ["BIGTREETECH-Octopus-Pro-V1.0-color-PIN-V3.0.jpg"](https://github.com/GadgetAngel/BTT_Octopus_Color_PIN_Diagram/blob/main/BTT_Octopus_Pro_V1.0_Color_PIN_Diagram/BIGTREETECH-Octopus-Pro-V1.0-color-PIN-V3.0.jpg) or ["BIGTREETECH-Octopus-Pro-V1.0-color-PIN-V3.0-400ppi.jpg"](https://github.com/GadgetAngel/BTT_Octopus_Color_PIN_Diagram/blob/main/BTT_Octopus_Pro_V1.0_Color_PIN_Diagram/BIGTREETECH-Octopus-Pro-V1.0-color-PIN-V3.0-400ppi.jpg) and then hit the download button.

Again, to download the PDF just click on the filename ["BIGTREETECH-Octopus-Pro-V1.0-Color-PIN-V3.0.pdf"](https://github.com/GadgetAngel/BTT_Octopus_Color_PIN_Diagram/blob/main/BTT_Octopus_Pro_V1.0_Color_PIN_Diagram/BIGTREETECH-Octopus-Pro-V1.0-Color-PIN-V3.0.pdf) or ["BIGTREETECH-Octopus-Pro-V1.0-Color-PIN-V3.0-400ppi.pdf"](https://github.com/GadgetAngel/BTT_Octopus_Color_PIN_Diagram/blob/main/BTT_Octopus_Pro_V1.0_Color_PIN_Diagram/BIGTREETECH-Octopus-Pro-V1.0-Color-PIN-V3.0-400ppi.pdf) and hit the download button.

JPG of Color PIN Diagram

## "Wiring_Harness_Diagram" for QUEEN:

This is the wiring harness diagram I developed for my Voron 2.4 build, it is also in the directory called "Wiring_Harness_Diagram".

Please take notice of the "Notes" section on the "Wiring_Harness_Diagram".

To ensure you see it, I am going to repeat it here:

```
Note about the Hartk1213 v3.rabbit board:
If the jumper pads on the back of the v3.rabbit are configured
incorrectly you could end up damaging your Octopus Pro mother board!!

Because there are two different versions of this Toolhead board around (let’s call them version #1,
and version #2), before powering on your printer, please ensure that the jumper pads on the back of
the v3.rabbit Toolhead board are properly configure for your FANS and ABL!

How to tell which version of the v3.rabbit Toolhead board you own:

If you turn the board over on its back, you will see a bank of jumper pads.  For version #1 of the
v3.rabbit Toolhead board has 4 columns by 3 rows of jumper pads.  For version #2 of v3.rabbit
Toolhead board has 3 columns by 3 rows of jumper pads.  If you have version #1 of the v3.rabbit
Toolhead board (4 columns by 3 rows of jumper pads) than you are responsible for bridging the
jumper pads to your desired voltage (in my case I would solder a bridge to 24VDC for ABL, PCF, HEF,
and FS).  If you have version #2 of the v3.rabbit Toolhead board (3 columns by 3 rows of jumper
pads) than all the selectable voltages default to 24VDC!

Here is what the labels mean:
ABL means auto bed leveling or an inductive probe or the proximity sensor connector;  PCF means
Part Cooling Fan; HEF means Hotend Fan; and FS means Filament Switch Sensor.

For version #1 of the v3.rabbit board, the columns are labeled from left to right: ABL, PCF, HEF,
FS. For version #2 of the v3.rabbit board, the columns are labeled from left to right: ABL, PCF,
HEF.

For version #1 and version #2 the rows are: 1st row is 24VDC; 2nd row is (ABL, PCF, or HEF, {only
on Version #1 FS}); and 3rd row is 5VDC.

If you have version #2 and you want 5VDC, you are going to cut the trace to the 24VDC on the
desired PIN (ABL, PCF or HEF)!
```

JPG of wiring harness Diagram

You can download the JPG file for this "Wiring_Harness_Diagram" by clicking on the filename ["Voron_2.4_Tool_Head_PCB__Wiring_Harness.jpg"](https://github.com/GadgetAngel/Voron2.4_My_Build_Log/blob/main/Wiring_Harness_Diagram/Voron_2.4_Tool_Head_PCB__Wiring_Harness.jpg).

 You can view an even higher resolution image (give it a minute or two to load, it takes longer due to the higher resolution) when you view the JPG in your browser by clicking on the filename ["Voron_2.4_Tool_Head_PCB__Wiring_Harness_400ppi.jpg"](https://github.com/GadgetAngel/Voron2.4_My_Build_Log/blob/main/Wiring_Harness_Diagram/Voron_2.4_Tool_Head_PCB__Wiring_Harness_400ppi.jpg) and then hit the download button.

## PDF version of the Wiring_Harness_Diagram":

You can view the PDF in your browser by clicking on the filename ["Voron_2.4_Tool_Head_PCB__Wiring_Harness.pdf"](https://github.com/GadgetAngel/Voron2.4_My_Build_Log/blob/main/Wiring_Harness_Diagram/Voron_2.4_Tool_Head_PCB__Wiring_Harness.pdf) and then hit the download button.

You can view an even higher resolution image (give it a minute or two to load, it takes longer due to the higher resolution) when you view the PDF in your browser by clicking on the filename ["Voron_2.4_Tool_Head_PCB__Wiring_Harness_400ppi.pdf"](https://github.com/GadgetAngel/Voron2.4_My_Build_Log/blob/main/Wiring_Harness_Diagram/Voron_2.4_Tool_Head_PCB__Wiring_Harness_400ppi.pdf) and then hit the download button.

## "Electronics_Case_Wiring_Diagram" directory you will find the wiring diagram for the electronics case for QUEEN:

Click here see the JPG file for the ["Voron 2.4 AC Electrical Wiring Diagram"](https://github.com/GadgetAngel/Voron2.4_My_Build_Log/tree/main/Electronics_Case_Wiring_Diagram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)

To download the PDF just click on the filename ["Voron_2.4_Electronics_Case_Wiring_Diagram_AC_wiring.pdf"](images/Voron_2.4_Electronics_Case_Wiring_Diagram_AC_wiring.pdf) and hit the download button.

## How Well Will Your Motors Perform on a Voron Build?

You need to look at the torque curve for your motors and see how your motors perform at different voltages.

Here is an Excel spreadsheet that can help you: https://github.com/eddietheengineer/documentation/tree/master/stepper_motor/data

To download the spreadsheet, just click on the file named ["motor_torque_sim_v7_database.xlsm"](https://github.com/eddietheengineer/documentation/blob/master/stepper_motor/data/motor_torque_sim_v7_database.xlsm) and hit the download button.

Once the Excel spreadsheet "motor_torque_sim_v7_database.xlsm" has downloaded, open it up in Excel but remember to "Enable" editing. If you do not enable editing you will not be able to see the "torque curve" graph. Also, the motors that are graphed can be chosen from a dropdown list. The voltage you run the stepper motors at can also be entered as can the current level.

Here are examples of Torque Curves produced by the Excel Spreadsheet:

As you will see when you go from 24V to 48V you can move faster. Also notice that when you go from 48V to 60V the gain is smaller than the jump from 24V to 48V!

Here is the Torque Curve for the specified stepper motors at 24 VDC:

Motor Torque Curve for 24V

Here is the Torque Curve for the same specified stepper motors at 48 VDC:

Motor Torque Curve for 48V

Here is the Torque Curve for the same specified stepper motors at 60 VDC:

Motor Torque Curve for 60V

As you can see when you go from 24V to 48V you can move faster. Also notice that when you go from 48V to 60V the gain is smaller than the jump from 24V to 48V!

## The Original BIGTREETECH Wiring Diagram for the Octopus Pro V1.0:

Original Wiring Diagram

## BIGTREETECH has a GitHub repository for the Octopus Pro V1.0:

The BIGTREETECH GitHub repository for Octopus Pro is located at https://github.com/bigtreetech/BIGTREETECH-OCTOPUS-Pro

## BIGTREETECH has a GitHub repository for the Octopus V1.0/1.1 Board:

The BIGTREETECH GitHub repository for Octopus 1.0/1.1 is located at https://github.com/bigtreetech/BIGTREETECH-OCTOPUS-V1.0

This repository also has information on how to wire up an Octopus V1.0/V1.1 board for a Voron Build and is located at https://github.com/bigtreetech/BIGTREETECH-OCTOPUS-V1.0/tree/master/Octopus%20works%20on%20Voron%20v2.4/Firmware

## How to set up Klipper on a Raspberry Pi

I am using a [Raspberry Pi 4B that I bought from CanaKit](https://www.canakit.com/raspberry-pi-4-extreme-aluminum-case-kit.html). You can choose to run the Raspberry Pi 4B with a micro-SD card, or you can use a solid state drive as your disk drive.

I bought a [Samsung 870 EVO 500 GB SATA (2.5") Solid State Drive (SSD) (MZ-77E500) from Amazon](https://www.amazon.com/gp/product/B08T1QQZ1T) with a [StarTech.com USB 3.1 to 2.5" SATA Hard Drive Adapter](https://www.amazon.com/gp/product/B00XLAZODE).

It does not matter which item you use to boot the Raspberry Pi 4B, but you do need at least a micro-SD card.

The first thing you will need to do is to format the micro-SD card or the SSD.  I have a Windows 10 machine so all my instructions will assume you are using a Windows 10 OS.

Before you can format a SSD you first need to initialize the media. On Window 10, "Right-click" on the startup menu in the lower left corner of your desktop. Choose the "Disk Management" option.  The "Disk Management" tool will automatically ask you if you want to initialize the new disk drive.  Say "Yes". When Windows is done, exit the "Disk Management" Tool. Now you need to create a primary partition for the SSD. Since we will be creating a primary partition of FAT32 larger than 32 GB, we can not use the Windows 10 "Disk Management" Tool to do this.

I like to use the program ["MiniTool Partion Wizard", so click here](https://www.partitionwizard.com/free-partition-manager.html). As a home user you can download it and use it for free. Download and Install the software onto your computer. With the "MiniTool Partion Wizard" you will need to create a primary partion by choosing the square labeled "Disk & Partition Management". Choose the new destination drive and select "Create a partition". Set "Create As" field to "Primary", set "File System" as "FAT32" and accept default for everything else. Select "Ok". Now all that did was place the command into the Que.  You need to select "Apply" to get the software to actually execute the command. Once "MiniTool Partion Wizard" is done creating the primary partion you can format the SSD by choosing the "Format Partition" and set the "File System" field to "FAT32". Leave all other fields at the default. Select "OK" and "Apply". When "MiniTool Partion Wizard" is finished you can exit the software by closing out the window.

For a micro-SD card, all you need to do is place the micro-SD card into an adapter that will allow your Windows 10 machine to read the micro-SD card. I need a micro-SD card to USB reader.  You can use windows to format the micro-SD card by opening Windows file explorer [Win Key]+[E key] select "This PC" now right-click on the micro-SD card and choose "Format". Set the "File System" field to "FAT32" and click "Start".

Once the micro-SD card (or SSD drive) is formatted for FAT32 you are ready to burn the image of "Raspberry Pi OS lite" onto the media. First you need to download the image of [Raspberry Pi OS Lite, by clicking here](https://www.raspberrypi.com/software/operating-systems/). Select "Download" next to the item listed as "Raspberry Pi OS Lite" and save the file onto your local disk drive. Remember where you put it because you will need to navigate to the image file in the next step. Before moving onto the next step take the time now to Un-Zip the folder, so you will be able to access the image (*.img) file.

Once the download is complete, you will need another program called ["Balena Etcher", so click here](https://www.balena.io/etcher/). Select "Download for Windows (x86|x64)" and save the file to your disk drive. Install the "Balena Etcher" software on to your computer.

Open Etcher and choose "Select Image". You now have to navigate to the directory of where you stored the image of "Raspberry Pi OS Lite. The name of the file for my "Raspberry Pi OS Lite" was "2021-10-30-raspios-bullseye-armhf-lite.img". Now choose "Select Drive". Since you formatted the micro-SD card (or the SSD) the media should have been assigned a disk drive letter. Ensure you have selected the correct drive letter.  You do not want to overwrite the wrong drive letter.  Disclaimer: I will not be held responsible for anyone who overwrites their main disk drive for their computer system.  Double check that you selected the correct drive letter and that it matches the one for your micro-SD card (or the SSD) that you will be using with your Raspberry Pi 4B. Once you are sure you have selected the correct drive letter, now select "Flash!". Etcher might give you a warning especially if you are flashing to a SSD, just again ensure you have the correct drive letter and when you are sure tell Etcher "yes or proceed".  Etcher will then take the *.img file and write it to the media. After Etcher is finished it will automatically dismount the media from your computer.  So unplug the USB connector of the micro-SD card (or SSD) and plug it back into your USB port.

We now have to add a file to the micro-SD card (or SSD).  This file is an empty file.  You just need to create the filename "SSH".  I usually just right-click inside the Window Explorer folder for the micro-SD card (or SSD) and choose the option of "New" → "Text document". I assign the name "SSH" and remove the extension ".txt".  This is a very important step the file CAN NOT have a file extension.  The file must be named "SSH" or "ssh" without an extension.  The empty ssh file will tell the "Raspberry Pi OS Lite" operating system to enable the SSH sever automatically upon first boot up.

Once you have added the ssh file to the contents of the micro-SD card (or SSD) it is now time to dismount the media from your computer and plug the media into the Raspberry Pi 4B, so it can boot up (of course you need to ensure you also connect a power supply to the Raspberry Pi 4B and an Ethernet cable).  Once you have plugged in the micro-SD card (or SSD) to the Raspberry Pi, and connect an Ethernet cable to the Ethernet port, turn on the power supply and allow it to boot.

The Raspberry Pi OS will look to see if a micro-SD card is present, if a micro-SD card is present it will try to boot off the micro-SD card. But if a micro-SD card is not present, it will start to look for another media to boot from and this is when it will find the solid state drive.  So for those of you that want to use the SSD as the main boot device make sure that the micro-SD card reader of your Raspberry Pi is empty when you have the SSD attached to the USB 3.0 port.

The Raspberry Pi will boot and then be assigned an IP address on your network.  We need to know the IP address, so we can remotely log in to the Raspberry Pi.  On a Windows 10 machine open up a command prompt window, and type the command "ping raspberrypi.local -4".  Since this is a fresh installation of the Raspberry Pi, all Raspberry Pi are assigned a hostname of raspberrypi after the initial boot.  The default login information is username is "pi" and password is "raspberry". After you perform the windows cmd "ping raspberrypi.local -4", the ping command will display an IP address that it transmitted packets too. Write down the IP address that received those packets.  This is the IP address of your new Raspberry Pi.

To set up Klipper on the new Raspberry Pi you will need to remotely log in into the Raspberry Pi via ssh.  To do this you need another software package called ["Putty", click here](https://www.putty.org/). Install the software on your computer. Now run Putty and enter the IP address (in the Host Name field) you saw in the "ping raspberrypi.local -4" command. Leave the Port number set to 22. Now hit "Open". You should see a window that pops up that says something about the authorization key has not been stored. Just say you trust the device. You will then get the login prompt. Enter in "pi" for the username and "raspberry" for the password.

If you get the "connect rejected" message, then there is something wrong with the ssh server. When you placed the empty ssh file in the file folder of the boot media you either misspelled the filename or left the ".txt" extension on the filename.  You can fix the "connect rejected" message by powering off the Raspberry Pi; removing the boot media from the Raspberry Pi; reattach the boot media to your computer and double-check the empty ssh filename is "ssh" only; then reattach the boot media to the Raspberry Pi and reboot again.

Now you should be logged in to the Raspberry Pi. When you see a "$" this means you need to type a command at the command prompt.  If you see a ">" this means you type a number at the current command prompt. Follow the below sequence to install KIAUH, Klipper, MoonRacker, Mainsail, KlipperScreen and Octoprint.  Once that is all installed we will then be hooking up the Octopus or Octopus Pro boards so that we can flash a new bootloader on to the boards. This new bootloader will allow the Raspberry Pi to talk to the Octopus board.  But for now just follow the below sequence to install everything you will need on the Raspberry Pi 4B. Also, make sure you have an Ethernet cable attached to the Raspberry Pi's Ethernet port:

```
$sudo raspi-config

The raspi-config Menu will be displayed.

>System Options -> change the system password (make note of the password so you do not forget it)
>System Options -> Boot/Autologin -> Console Autologin; turn this on
>System Option -> Network at Boot; turn this on
>Interface Options -> turn on camera interface
>Interface Options -> turn on SSH
>Localization Options -> set Time Zone for your area -> for me USA: Eastern Time
>Localization Options -> set Localization -> if in USA use "en_US.UTF-8"
>Localization Options -> WLAN Country -> set this to your country -> for me USA
>Advanced Options -> expand filesystem
>Finish

$sudo reboot

Now wait for the device to reboot and use Putty to log back into the Raspberry pi and continue onto the next step

$sudo apt update
$sudo apt full-upgrade
$sudo apt autoremove
sudo apt-get install git -y
$cd ~
$git clone https://github.com/th33xitus/kiauh.git
$./kiauh/kiauh.sh

The KIAUH menu will appear.

>1
>1
>2

make a note of the Moonracker Instance (write down the IP address)

>3

make a note of the MJPG-Streamer webcam URLs

>5
>7

make a note of the Octoprint IP address

>B
>Q

```
Now that Klipper and its corresponding software has been installed onto the Raspberry Pi, I want to do a clean reboot before we go onto the next step of compiling the Klipper firmware and updating the mother board (Octopus or Octopus Pro board).

```
$sudo reboot
```

If you have either an Octopus V1.0/V1.1 board or the Octopus PRO board you will need a fresh micro-SD card so that you can transfer the compiled firmware over to the Octopus V1.0/V1.1 board or the Octopus PRO board. You will need to download and install on your PC the software ["winscp", by clicking here](https://winscp.net/eng/download.php). 

The Winscp software will allow you to transfer a file off the Raspberry Pi to your PC's disk drive. This way when the Raspberry Pi has finished compiling the firmware for the Octopus board you can grab the "Klipper.bin" file and transfer it to your PC disk drive and then copy it over to the Micro-SD card that you will place into the Octopus board's Micro-SD card reader.  When you copy the "klipper.bin" file over to the Micro-SD card remember to rename it to "firmware.bin". If the file is not renamed "firmware.bin" then the Octopus boards (V1.0/V1.1 or PRO) bootloader will not be updated properly.

Now we need to apply power to the Octopus board.  I typically power the Octopus board using the USB-C cable when I do this next step (ensure you have the Jumper on the for PWR SELECTION header so that the USB-C can power the 5V rail of the Octopus board)

But you could power the Octopus board by using an independent PSU and attach the 12VDC and GND to the screw terminals (just ensure you **remove** the Jumper from the PWR SELECTION header so that the 5V rail is **not** getting power via the USB-C cable)

Now use the USB-C cable that came with the Octopus board and attach it to the Raspberry Pi (USB 2.0) port.  If the Jumper is on the PWR SELECTION header than the Raspberry Pi will supply the 5VDC to the 5V rail of the Octopus Board and also communicate to the Octopus board via USB. If the Jumper is removed from the PWR SELECTION header than the USB-C cable will be used for communications only.

When the Raspberry Pi reboots, use Putty to log back into the device.

If you have an Octopus V1.0/V1.1 board follow the steps below (skip these steps if you have an Octopus Pro board with the F446 chip or the F429 chip):

```
$./kiauh/kiauh.sh

The KIAUH menu will appear.

>4
>3

[*] Enable extra low-level configuration options by moving the cursor and hitting the space bar until the "*" appears.

The space bar is a toggle so when the "*" appears it means you have selected the item.
When the  "*" is not present it means the item is NOT selected. You use the arrow keys on your keyboard to move up and down the menu.

set Micro-controller Architecture to (STMicroelectronics STM32)
set Processor model to (STM32F446)
set Bootloader offset to (32KiB bootloader)
set Clock Reference to (12 Mhz crystal)
set Communication interface to (USB (on PA11/PA12))
>Q Y

The firmware will compile.

>B
>Q

You will now have to use a micro-SD card to flash the Octopus board with the new firmware. The Octopus board will not 
update the firmware via USB cable! After you have copied the out\Klipper.bin file over to your PC (using Winscp) and onto 
the micro-SD card, please rename the "klipper.bin" file to "firmware.bin".  Once you place the micro-SD card into the 
Octopus board's Micro-SD card reader it will update its bootloader. To ensure that the board really did update the 
bootloader pull the micro-SD card out of the Octopus board and reload it onto your PC. Check to see if the filename has 
been change from "firmware.bin" to "FIRMWARE.CUR".  If the filename changed then the Octopus board updated its bootloader correctly.

```

If you have an Octopus V1.0/V1.1 board or the Octopus Pro board with the F429 chip, skip the following steps.  These steps are for the Octopus PRO board with the F446 chip. If you have an Octopus Pro board that uses the F446 chip, please follow the next steps:

```
$./kiauh/kiauh.sh

The KIAUH menu will appear.

>4
>3

[*] Enable extra low-level configuration options by moving the cursor and hitting the space bar until the "*" appears.

The space bar is a toggle so when the "*" appears it means you have selected the item
when the  "*" is not present it means the item is NOT selected. You use the arrow keys on your keyboard to move up and down the menu.

set Micro-controller Architecture to (STMicroelectronics STM32)
set Processor model to (STM32F446)
set Bootloader offset to (32KiB bootloader)
set Clock Reference to (12 Mhz crystal)
set Communication interface to (USB (on PA11/PA12))
>Q Y

The firmware will compile.

>B
>Q

You will now have to use a micro-SD card to flash the Octopus board with the new firmware. The Octopus board will not 
update the firmware via USB cable! After you have copied the out\Klipper.bin file over to your PC (using Winscp) and onto 
the micro-SD card, please rename the "klipper.bin" file to "firmware.bin".  Once you place the micro-SD card into the 
Octopus board's Micro-SD card reader it will update its bootloader. To ensure that the board really did update the 
bootloader pull the micro-SD card out of the Octopus board and reload it onto your PC. Check to see if the filename has 
been change from "firmware.bin" to "FIRMWARE.CUR".  If the filename changed then the Octopus board updated its bootloader correctly.
```

If you have an Octopus V1.0/V1.1 board or an Octopus Pro board with F446 chip, skip the following steps. These steps are for the Octopus PRO board with the F429. If you have an Octopus Pro board that uses the F429 chip, please follow the next steps:

```
$./kiauh/kiauh.sh

The KIAUH menu will appear.

>4
>3

[*] Enable extra low-level configuration options by moving the cursor and hitting the space bar until the "*" appears.

The space bar is a toggle so when the "*" appears it means you have selected the item
when the  "*" is not present it means the item is NOT selected. You use the arrow keys on your keyboard to move up and down the menu.

set Micro-controller Architecture to (STMicroelectronics STM32)
set Processor model to (STM32F429)
set Bootloader offset to (32KiB bootloader)
set Clock Reference to (8 Mhz crystal)
set Communication interface to (USB (on PA11/PA12))
>Q Y

The firmware will compile.

>B
>Q

You will now have to use a micro-SD card to flash the Octopus board with the new firmware. The Octopus board will not 
update the firmware via USB cable! After you have copied the out\Klipper.bin file over to your PC (using Winscp) and onto 
the micro-SD card, please rename the "klipper.bin" file to "firmware.bin".  Once you place the micro-SD card into the 
Octopus board's Micro-SD card reader it will update its bootloader. To ensure that the board really did update the 
bootloader pull the micro-SD card out of the Octopus board and reload it onto your PC. Check to see if the filename has 
been change from "firmware.bin" to "FIRMWARE.CUR".  If the filename changed then the Octopus board updated its bootloader correctly.

```

### Finding the MCU ID:

At this point if you have an Octopus V1.0/V1.1 or an Octopus Pro with F446 chip or an Octopus Pro with F429 Chip, you have successfully updated its bootloader because the "firmware.bin" filename on the micro-SD card was renamed to "FIRMWARE.CUR"

But we will be needing the MCU ID for out Klipper configuration file, so let's log back into the Raspberry Pi by using Putty.

Now power the Octopus board via which USB-C or with an independent power supply. Connect the USB-C cable from the Octopus board to the Raspberry Pi's USB 2.0 port. We need to find the ID for this connection.

Please do the following:

```
$./kiauh/kiauh.sh

The KIAUH menu will appear.

>4
>6
>1

the menu will refresh, but, **above the menu** you will see something similar to my output (each Octopus board will generate a unique id).

● (USB) MCU #1: /dev/serial/by-id/usb-Klipper_stm32f446xx_3B001B00115053424E363620-if00

Copy this string down because you will have to add it to your Klipper config file later.

>B
>Q
```

If you loose the MCU ID you can always rerun KIAUH option 4, option 6, choose 1 for USB, and it will display the information for you again.

## Klipper firmware supports the Octopus Pro V1.0 board:

Here is the link to the config file on GitHub for the Octopus pro V1.0 board https://github.com/Klipper3d/klipper/blob/master/config/generic-bigtreetech-octopus.cfg.

Here is the link to the Klipper configuration file for the Voron 2.4 printer on the Voron 2.4 GitHub site https://github.com/VoronDesign/Voron-2/blob/Voron2.4/firmware/klipper_configurations/Octopus/Voron2_Octopus_Config.cfg

If you are using the "PROBE" connector for a proximity sensor you will need to add a [probe] section to the "generic-bigtreetech-octopus.cfg" file and ensure that the sensor_pin: PC5

There is only two PINs that are different between the Octopus V1.1 pin-out and the Octopus Pro V1.0 pin-out. The Octopus V1.1 pin-out has PC5 on the EXP2 connector but on the Octopus Pro V1.0 this pin on the EXP2 connector is now "Not Connected (NC)".

The second PIN difference is that on the Octopus V1.1 pin-out PB7 is the signal PIN used on the PROBE/SENSOR connector and on the BLTouch header but on the Octopus Pro V1.0 the signal pin on the PROBE connector is PC5.  Which means that on the Octopus V1.1 board you can only use either a BLTouch or a Proximity Sensor but NOT both. On the Octopus Pro V1.0 since the signal pins for the PROBE connector is different from the BLTouch, if you wanted to, you could use both ports.

If you plan to use a voltage higher than 24V on MOTOR_POWER_IN then please pay attention to the footnote #1 on the "Color PIN Diagram".

You may need to change the Fuse on the MB_POWER_IN. To calculate the maximum amps you will be using on the MB_POWER_IN connection you will need to know the maximum amps allowed on the 24VDC rail for the motherboard.

To calculate the maximum amps allowed on the 24VDC rail on mother board:

 (the four heaters {HE0-HE3}, 3.3VDC rail, 5VDC rail, and 12VDC rail are all produced from the 24VDC rail).

 The maximum amps for 3.3VDC rail is 1 Amp.

 The maximum amps for the 5VDC rail is 8 Amps.

 The maximum amps for 12VDC rail is 4 Amps.

 So the total maximum amps for 3.3VDC rail + 5VDC rail + 12VDC rail is equal to 13 Amps, but the amps needed to run the four heaters needs to be added to this value.

 Since BIGTREETECH supplies us with a 20 Amp fuse, then BIGTREETECH is saying that you have 7 more Amps available for all four heater ports or 1.75 Amps / heater cartridge. Just do not use more than 7 Amps on any combination of the four heater {HE0-HE3} ports!

Please use the "Color PIN Diagram" in [BTT_Octopus_Pro_V1.0_Color_PIN_Diagram](https://github.com/GadgetAngel/BTT_Octopus_Color_PIN_Diagram/tree/main/BTT_Octopus_Pro_V1.0_Color_PIN_Diagram) to obtain the correct PIN assignments.

If you decide to flash a new bootloader to the Octopus Pro V1.0 board (you should not need to because you can upload the new Klipper firmware using the micro-SD card reader) and find that the micro-SD card bootloader no longer works you will want to return the board to its shipment state by finding the original bootloader and "bootloader+firmware" files at https://github.com/GadgetAngel/BTT_SKR_13_14_14T_SD-DFU-Bootloader/tree/main/bootloader_bin/backed_up_original_bootloaders

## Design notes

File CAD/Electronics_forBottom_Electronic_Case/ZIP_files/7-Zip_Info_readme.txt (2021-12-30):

7-Zip 21.07
-----------

7-Zip is a file archiver for Windows.

7-Zip Copyright (C) 1999-2021 Igor Pavlov.

The main features of 7-Zip: 

  - High compression ratio in the new 7z format
  - Supported formats:
     - Packing / unpacking: 7z, XZ, BZIP2, GZIP, TAR, ZIP and WIM.
     - Unpacking only: AR, ARJ, Base64, CAB, CHM, CPIO, CramFS, DMG, EXT, FAT, GPT, HFS,
                       IHEX, ISO, LZH, LZMA, MBR, MSI, NSIS, NTFS, QCOW2, RAR, 
                       RPM, SquashFS, UDF, UEFI, VDI, VHD, VHDX, VMDK, XAR and Z.
  - Fast compression and decompression
  - Self-extracting capability for 7z format
  - Strong AES-256 encryption in 7z and ZIP formats
  - Integration with Windows Shell
  - Powerful File Manager
  - Powerful command line version
  - Localizations for 90 languages

7-Zip is free software distributed under the GNU LGPL (except for unRar code).
Read License.txt for more information about license.

  This distribution package contains the following files:

  7zFM.exe      - 7-Zip File Manager
  7-zip.dll     - Plugin for Windows Shell
  7-zip32.dll   - Plugin for Windows Shell (32-bit plugin for 64-bit system) 
  7zg.exe       - GUI module
  7z.exe        - Command line version
  7z.dll        - 7-Zip engine module
  7z.sfx        - SFX module (Windows version)
  7zCon.sfx     - SFX module (Console version)

  License.txt   - License information
  readme.txt    - This file
  History.txt   - History of 7-Zip
  7-zip.chm     - User's Manual in HTML Help format
  descript.ion  - Description for files

  Lang\en.ttt   - English (base) localization file
  Lang\*.txt    - Localization files

---
End of document

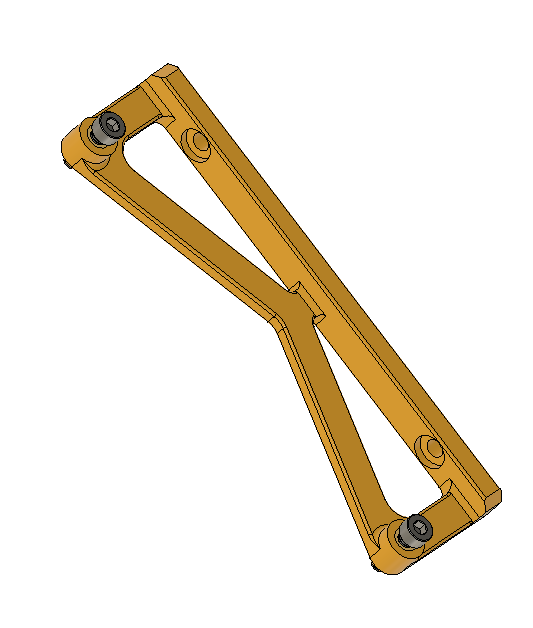
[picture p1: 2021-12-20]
The_.STL_Files/GA_modded_STLs/LitterBox_Mod/Electronics/Klipper_Expander_Board/Extrusion_Mounts/90-Degree/Klipper_Expander_mount_90-Degree_Extrusion_mount.png

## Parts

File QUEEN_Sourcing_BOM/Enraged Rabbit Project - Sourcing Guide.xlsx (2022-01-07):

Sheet: Carrot Feeder
Sourcing Guide for Ette's Enraged Rabbit : Carrot Feeder
BOM for the Enraged Rabbit Carrot Feeder V1.1! This is for a N channels system (if you want 6 filaments then replace N by 6). This doesn't include the BOM for the toolhead sensor (for that look on the other tabs)!
# Channels | 9 | Number of channels |  |  |  | ALL ALI EXPRESS LINKS ARE AFFILIATED =)
 | Component | Spec | Size/Length/ variable qty | Qty | All sizes | Source 1 | Source 2 | Source 3 | Source 4 | Notes
Electronics | NEMA14 Motor 14HS11-1004S |  |  | 1 | All | Stepper Online (https://www.omc-stepperonline.com/nema-14-bipolar-1-8deg-12-5ncm-17-7oz-in-1a-3-5v-35x35x28mm-4-wires.html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) | Aliexpress (https://www.aliexpress.com/item/33015617147.html)
Electronics | NEMA17 Motor 17HS08-1004S |  |  | 1 | All | Stepper Online (https://www.omc-stepperonline.com/nema-17-stepper-motor/nema-17-bipolar-1-8deg-16ncm-22-6oz-in-1a-3-7v-42x42x20mm-4-wires.html) | Stepper Online (Ali) (https://s.click.aliexpress.com/e/_AoYqnK) | Amazon DE (https://www.amazon.de/STEPPERONLINE-Schrittmotor-Bipolar-42x42x20mm-4-Dr%C3%A4hte/dp/B06XVM38YW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)
Electronics | towerpro MG90S servo |  |  | 1 | All | Amazon US (https://www.amazon.com/Maxmoral-Upgraded-Digital-Vehicle-Helicopter/dp/B07NV476P7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) | Amazon FR (https://amzn.to/3E7eDK3) | Amazon DE (https://www.amazon.de/ZHITING-MG90S-Metallgetriebe-Hubschrauber-Flugzeug/dp/B088NQM7XW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) | Aliexpress (https://s.click.aliexpress.com/e/_AONF2h) | Knock off will work
Electronics | Stepper drivers (any, but TMC2209 are nice) |  |  | 2 |  | Aliexpress (https://s.click.aliexpress.com/e/_A3ZzxA) | Amazon US (https://www.amazon.com/BIGTREETECH-TMC2209-Stepper-Printer-Motherboard/dp/B08SMDY3SQ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) | Amazon FR (https://amzn.to/3la60G6) | Amazon DE (https://www.amazon.de/KINGPRINT-TMC2209-Stepper-Driver-Printer/dp/B07WC71M4R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) | should have left over from 2.4BOM
Electronics | TCRT5000 sensor pcb |  |  | 1 |  | Amazon US (https://www.amazon.com/SUBALIGU-TCRT5000-Infrared-Follower-Avoidance/dp/B08HLW4PPD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) |  | Aliexpress (https://s.click.aliexpress.com/e/_ADrfkY) |  | There are many versions. The black PCB is mandatory. Try to get the version with the off-centered hole rather than the center one.
Electronics | Omron Mouse Button - Micro Switch |  |  | 1 |  | Digikey (https://www.digikey.com/product-detail/en/omron-electronics-inc-emc-div/D2F-5L/Z8846-ND/8593137)
Hardware | N sets of bondtechs gears | qty = N + 1 | 10 | Variable |  | TwoTrees (https://s.click.aliexpress.com/e/_A7mydO)
Hardware | LM8UU bearings or RJ4JP-01-08 | 8mm |  | 2 |  | TriangleLab (https://s.click.aliexpress.com/e/_9xJ8NI)
Hardware | M5 threaded rods | Length = 25 + N*21 + ceil(N/3 -1)*5 mm | 224 | 2 |  | Aliexpress (https://s.click.aliexpress.com/e/_A4l008) |  |  |  | You can also find it at your local hardware stores.
Hardware | 8mm smooth rods | Length = 40 + N*21 + ceil(N/3 - 1)*5 mm | 239 | 2 |  | TwoTrees (https://s.click.aliexpress.com/e/_9uJaVm) |  |  |  | You can also find it at your local hardware stores.
Hardware | D-cut 5mm shaft | Length = 70 + N*21 + ceil(N/3 - 1)*5 mm | 269 | 1 |  | POWGE (https://s.click.aliexpress.com/e/_ABzAlO) | AliExpress FULL, NO D-CUT (https://s.click.aliexpress.com/e/_AefrTe) |  |  | Powge can sell shafts with the D-cut already, but it's bertween 10€ and 20€ for 1 shaft; which is quite expensive. You can order a round 5mm shaft elsewhere (for like 2€) and do the D cuts yourself, this is a much cheaper option
Hardware | MR623ZZ bearing |  |  | 1 | All | TriangleLab (https://s.click.aliexpress.com/e/_9ikulA)
Hardware | MR85ZZ bearings | qty = 4 + ceil(N/3 - 1) | 6 | Variable |  | TriangleLab (https://s.click.aliexpress.com/e/_AfBHbm)
Fasteners | M3 threaded inserts | M3x5x4mm. qty = 26 |  | 26 | All | Aliexpress - M3x5x4 (https://s.click.aliexpress.com/e/_AavdJq)
Fasteners | M5x30 BHCS |  |  | 2 |  | Bolt Depot (https://www.boltdepot.com/Product-Details.aspx?product=15651) | McMaster-Carr (100 pack) (https://www.mcmaster.com/91239A236)
Fasteners | M5x16 BHCS |  |  | 1 |  | Bolt Depot (https://www.boltdepot.com/Product-Details.aspx?product=15648) | McMaster-Carr (100 pack) (https://www.mcmaster.com/91239A232)
Fasteners | M5 nuts |  |  | 4
Fasteners | M5 nylock nuts |  |  | 5
Fasteners | M5 washers | whatever thickness |  | 2
Fasteners | M3x8 SHCS |  |  | 20 |  | Bolt Depot (https://www.boltdepot.com/Product-Details.aspx?product=13635) | McMaster-Carr (100 pack) (https://www.mcmaster.com/91290a113)
Fasteners | M3x8 BHCS |  |  | 5
Fasteners | M3x12 SHCS |  |  | 3 |  | Bolt Depot (https://www.boltdepot.com/Product-Details.aspx?product=13637) | McMaster-Carr (100 pack) (https://www.mcmaster.com/91290A117)
Fasteners | M3x16 SHCS | qty = 4 + N | 13 | Variable |  | Bolt Depot (https://www.boltdepot.com/Product-Details.aspx?product=13638) | McMaster-Carr (100 pack) (https://www.mcmaster.com/91290A120)
Fasteners | M3x20 SHCS |  |  | 7
Fasteners | M3x40 SHCS |  |  | 2
Fasteners | M3 washers (could also be the DIN125 below) | whatever thickness |  | 2
Fasteners | M3 DIN125 Steel Washer | 7mm Outer diameter, 0.5mm thickness STEEL | 9 | Variable |  | Bolt Depot (https://www.boltdepot.com/Product-Details.aspx?product=4524) |  |  |  | We need those to be magnetic. Stainless Steel WON'T work
Fasteners | M2x8 SHCS or M2x10 SHCS |  |  | 2
Motion | GT2 belt 6mm (open) | Length = 150 + N*42 + ceil(N/3 - 1)*10 mm | 548 | 1 |  | POWGE (https://s.click.aliexpress.com/e/_AFoHHw)
Motion | GT2 20T Pulley 6 mm, 5mm bore |  |  | 3 |  | POWGE (https://s.click.aliexpress.com/e/_9u6cA0)
Motion | GT2 20T Toothed Idler 6 mm, 5mm bore |  |  | 1 |  | POWGE (https://s.click.aliexpress.com/e/_APR41m)
Motion | GT2 188m Belt loop 6mm |  |  | 1 |  | POWGE (https://s.click.aliexpress.com/e/_AoQ8jE)
Misc | 6mm x 3mm Round Neodymium Magnets | 6x3mm. qty = 4 + Nx3 | 31 | Variable |  | Aliexpress (https://s.click.aliexpress.com/e/_A00Gse) |  |  |  | should have left over from 2.4BOM
Misc | Bowden Clip | qty = 1 + N | 10 | Variable |  | TriangleLab (https://s.click.aliexpress.com/e/_ADrrha)
Misc | Bowden Fitting | qty = 1 + N | 10 | Variable |  | TriangleLab (https://s.click.aliexpress.com/e/_AW9RVK)
Misc | 7X7 Drag chain |  |  | 1 |  | TwoTress (https://s.click.aliexpress.com/e/_A4lTBQ)
Cables | MicroFit3 Male Pin (43031-0007) |  |  | 26
Cables | MicroFit3 Female Pin (43030-0007) |  |  | 26
Cables | MicroFit Connector Receptacle 4 Position (43645-0400) |  |  | 4
Cables | MicroFit Connector Plug 4 Position (43640-0401) |  |  | 4
Cables | MicroFit Connector Receptacle 5 Position (43645-0500) |  |  | 2
Cables | MicroFit Connector Plug 5 Position (43640-0501) |  |  | 2

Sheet: Carrot Patch
Sourcing Guide for Ette's Enraged Rabbit : Carrot Patch
This is for a single spool holder |  |  |  |  |  | ALL ALI EXPRESS LINKS ARE AFFILIATED =)
 | Component | Spec | Size/Length | Qty | All sizes | Recommended |  | Notes
Hardware | 608ZZ bearing |  |  | 1
Fasteners | M3 threaded inserts | M3x5x4mm |  | 4 |  | Aliexpress - M3x5x4 (https://s.click.aliexpress.com/e/_AavdJq)
Fasteners | M5x30 BHCS |  |  | 1 |  | Bolt Depot (https://www.boltdepot.com/Product-Details.aspx?product=15651) | McMaster-Carr (100 pack) (https://www.mcmaster.com/91239A236)
Fasteners | M5 nylock nuts |  |  | 1
Fasteners | M3x8 SHCS |  |  | 2 |  | Bolt Depot (https://www.boltdepot.com/Product-Details.aspx?product=13635) | McMaster-Carr (100 pack) (https://www.mcmaster.com/91290a113)
Fasteners | M3x16 SHCS |  |  | 1
Fasteners | M3X20 SHCS |  |  | 1
Misc | PTFE tubing 2.5 mm ID 4 mm OD |  | ~40cm | 1 |  | Aliexpress (https://s.click.aliexpress.com/e/_APSGDe)
Option 1 : Only use ECAS connectors. Use either Option 1 or 2
Misc | Bowden Clip |  |  | 2 |  | TriangleLab (https://s.click.aliexpress.com/e/_AeTnAk)
Misc | Bowden Fitting |  |  | 2 |  | TriangleLab (https://s.click.aliexpress.com/e/_9I62Mc)
Option 2 : 1 ECAS connector and 1 M10 ptfe pressfit (with the ptfe tube going through). Use either Option 1 or 2
Misc | M10 PTFE pressFit (ptfe goes through) |  |  | 1
Misc | Bowden Clip |  |  | 1 |  | TriangleLab (https://s.click.aliexpress.com/e/_AeTnAk)
Misc | Bowden Fitting |  |  | 1 |  | TriangleLab (https://s.click.aliexpress.com/e/_9I62Mc)

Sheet: Toolhead Sensor
Sourcing Guide for Ette's Enraged Rabbit : Toolhead sensor (New Tircown's design!)
This is for a single toolhead sensor (BOM is the same for AB, Galileo and LGX extruders) |  |  |  |  |  | ALL ALI EXPRESS LINKS ARE AFFILIATED =)
 | Component | Spec | Size/Length | Qty | All sizes | Recommended | Notes
Electronics | AH3364Q-P-B Hall Effect sensor (SIP) |  |  | 1 |  | Digikey (https://www.digikey.com/en/products/detail/diodes-incorporated/AH3364Q-P-B/6575180) | Get the SIP3 housing version, not the SMD one. You can also use the AH3364Q-P-A, difference will be in the packaging and the legs shape
Fasteners | M3 DIN125 Steel Washer | 7mm Outer diameter, 0.5mm thickness STEEL |  | 1 |  | Bolt Depot (https://www.boltdepot.com/Product-Details.aspx?product=4524) | We need those to be magnetic. Stainless Steel WON'T work
Misc | 6mm x 3mm Round Neodymium Magnets |  |  | 1 |  | Aliexpress (https://s.click.aliexpress.com/e/_A00Gse)
Fasteners | M3x8 SHCS |  |  | 1
Fasteners | M3x12 SHCS |  |  | 1
Option 1 : Galileo Clockwork toolhead
Optionnal | JST XH 3 pins male connector |  |  | 1 |  | Digikey (https://www.digikey.com/en/products/detail/jst-sales-america-inc/B3B-XH-AM-LF-SN/1651029) | You can use whatever kind of connector you prefer, but the JST XH can be inserted into the Galileo main body

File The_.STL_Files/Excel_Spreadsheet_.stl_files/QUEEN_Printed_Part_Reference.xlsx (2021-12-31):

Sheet: Original V2.4 PrintedPartRef
Location |  |  |  |  | Part | Color | Quantity | Essential (PIF provided) | Non-Essential | Notes
Electronics_Compartment (https://github.com/VoronDesign/Voron-2/blob/Voron2.4/STLs/VORON2.4/Electronics_Compartment/DIN_Brackets/duet_duex_bracket_x2.stl) | DIN_Brackets |  |  |  | duet_duex_bracket_x2 | Primary | 2 | Included - Choose one
Electronics_Compartment (https://github.com/VoronDesign/Voron-2/blob/Voron2.4/STLs/VORON2.4/Electronics_Compartment/DIN_Brackets/ramps_bracket_x2.stl) | DIN_Brackets |  |  |  | ramps_bracket_x2 | Primary | 2
Electronics_Compartment (https://github.com/VoronDesign/Voron-2/blob/Voron2.4/STLs/VORON2.4/Electronics_Compartment/DIN_Brackets/skr_1.3_1.4_bracket_x2.stl) | DIN_Brackets |  |  |  | skr_1.3_1.4_bracket_x2 | Primary | 2
Electronics_Compartment (https://github.com/VoronDesign/Voron-2/blob/Voron2.4/STLs/VORON2.4/Electronics_Compartment/DIN_Brackets/skr_mini_e3_bracket_x2.stl) | DIN_Brackets |  |  |  | skr_mini_e3_bracket_x2 | Primary | 2
 |  |  |  |  | spider bracket | Primary | 1 |  |  | PIF option, not in main repo at this time
 |  |  |  |  | octopus bracket | Primary | 1 |  |  | PIF option, not in main repo at this time
Electronics_Compartment (https://github.com/VoronDesign/Voron-2/blob/Voron2.4/STLs/VORON2.4/Electronics_Compartment/DIN_Brackets/lrs_psu_bracket_clip.stl) | DIN_Brackets |  |  |  | lrs_psu_bracket_clip | Primary | 1 | Included
Electronics_Compartment (https://github.com/VoronDesign/Voron-2/blob/Voron2.4/STLs/VORON2.4/Electronics_Compartment/DIN_Brackets/pcb_din_clip_x3.stl) | DIN_Brackets |  |  |  | pcb_din_clip_x3 | Primary | 3 | Included
Electronics_Compartment (https://github.com/VoronDesign/Voron-2/blob/Voron2.4/STLs/VORON2.4/Electronics_Compartment/DIN_Brackets/raspberrypi_bracket.stl) | DIN_Brackets |  |  |  | raspberrypi_bracket | Primary | 1 | Included
Electronics_Compartment (https://github.com/VoronDesign/Voron-2/blob/Voron2.4/STLs/VORON2.4/Electronics_Compartment/DIN_Brackets/rs25_psu_bracket_clip.stl) | DIN_Brackets |  |  |  | rs25_psu_bracket_clip | Primary | 1 | Included
Electronics_Compartment (https://github.com/VoronDesign/Voron-2/blob/Voron2.4/STLs/VORON2.4/Electronics_Compartment/LCD_Module/%5Ba%5D_mini12864_case_hinge.stl) | LCD_Module |  |  |  | [a]_mini12864_case_hinge | Alternate | 1 |  | Optional
Electronics_Compartment (https://github.com/VoronDesign/Voron-2/blob/Voron2.4/STLs/VORON2.4/Electronics_Compartment/LCD_Module/mini12864_case_front.stl) | LCD_Module |  |  |  | mini12864_case_front | Primary | 1 |  | Optional
Electronics_Compartment (https://github.com/VoronDesign/Voron-2/blob/Voron2.4/STLs/VORON2.4/Electronics_Compartment/LCD_Module/mini12864_case_rear.stl) | LCD_Module |  |  |  | mini12864_case_rear | Primary | 1 |  | Optional
Electronics_Compartment (https://github.com/VoronDesign/Voron-2/blob/Voron2.4/STLs/VORON2.4/Electronics_Compartment/LCD_Module/mini12864_spacer.stl) | LCD_Module |  |  |  | mini12864_spacer | Primary | 1 |  | Optional
Electronics_Compartment (https://github.com/VoronDesign/Voron-2/blob/Voron2.4/STLs/VORON2.4/Electronics_Compartment/Legacy_Brackets/dual_ramps_bracket_legacy.stl) | Legacy_Brackets |  |  |  | dual_ramps_bracket_legacy | Primary | 1 |  | Optional
Electronics_Compartment (https://github.com/VoronDesign/Voron-2/blob/Voron2.4/STLs/VORON2.4/Electronics_Compartment/Legacy_Brackets/duet_duex_bracket_legacy_x2.stl) | Legacy_Brackets |  |  |  | duet_duex_bracket_legacy_x2 | Primary | 2 |  | Optional
Electronics_Compartment (https://github.com/VoronDesign/Voron-2/blob/Voron2.4/STLs/VORON2.4/Electronics_Compartment/Legacy_Brackets/lrs_bracket_legacy.stl) | Legacy_Brackets |  |  |  | lrs_bracket_legacy | Primary | 1 |  | Optional
Electronics_Compartment (https://github.com/VoronDesign/Voron-2/blob/Voron2.4/STLs/VORON2.4/Electronics_Compartment/Legacy_Brackets/mks_gen_1.4_bracket_legacy_x2.stl) | Legacy_Brackets |  |  |  | mks_gen_1.4_bracket_legacy_x2 | Primary | 2 |  | Optional
Electronics_Compartment (https://github.com/VoronDesign/Voron-2/blob/Voron2.4/STLs/VORON2.4/Electronics_Compartment/Legacy_Brackets/mks_gen_L_bracket_legacy_x2.stl) | Legacy_Brackets |  |  |  | mks_gen_L_bracket_legacy_x2 | Primary | 2 |  | Optional
Electronics_Compartment (https://github.com/VoronDesign/Voron-2/blob/Voron2.4/STLs/VORON2.4/Electronics_Compartment/Legacy_Brackets/raspberry_pi_bracket.stl) | Legacy_Brackets |  |  |  | raspberry_pi_bracket | Primary | 1 |  | Optional
Electronics_Compartment (https://github.com/VoronDesign/Voron-2/blob/Voron2.4/STLs/VORON2.4/Electronics_Compartment/Legacy_Brackets/rs_25_psu_bracket_legacy.stl) | Legacy_Brackets |  |  |  | rs_25_psu_bracket_legacy | Primary | 1 |  | Optional
Electronics_Compartment (https://github.com/VoronDesign/Voron-2/blob/Voron2.4/STLs/VORON2.4/Electronics_Compartment/Legacy_Brackets/rs_35_bracket_legacy.stl) | Legacy_Brackets |  |  |  | rs_35_bracket_legacy | Primary | 1 |  | Optional
Electronics_Compartment (https://github.com/VoronDesign/Voron-2/blob/Voron2.4/STLs/VORON2.4/Electronics_Compartment/Legacy_Brackets/skr_1.3_bracket_legacy.stl) | Legacy_Brackets |  |  |  | skr_1.3_bracket_legacy | Primary | 1 |  | Optional
Electronics_Compartment (https://github.com/VoronDesign/Voron-2/blob/Voron2.4/STLs/VORON2.4/Electronics_Compartment/Legacy_Brackets/skr_mini_e3_bracket_legacy.stl) | Legacy_Brackets |  |  |  | skr_mini_e3_bracket_legacy | Primary | 1 |  | Optional
Electronics_Compartment (https://github.com/VoronDesign/Voron-2/blob/Voron2.4/STLs/VORON2.4/Electronics_Compartment/Plug_Panel/%5Ba%5D_keystone_blank_insert.stl) | Plug_Panel |  |  |  | [a]_keystone_blank_insert | Alternate | 1 |  | Optional
Electronics_Compartment (https://github.com/VoronDesign/Voron-2/blob/Voron2.4/STLs/VORON2.4/Electronics_Compartment/Plug_Panel/plug_panel.stl) | Plug_Panel |  |  |  | plug_panel | Primary | 1 |  | Optional | Only one needed, choose one. For PIF check with provider.
Electronics_Compartment (https://github.com/VoronDesign/Voron-2/blob/Voron2.4/STLs/VORON2.4/Electronics_Compartment/Plug_Panel/plug_panel_filtered_mains.stl) | Plug_Panel |  |  |  | plug_panel_filtered_mains | Primary | 1 | Included
Exhaust_Filter (https://github.com/VoronDesign/Voron-2/blob/Voron2.4/STLs/VORON2.4/Exhaust_Filter/%5Ba%5D_exhaust_filter_mount_x2.stl) |  |  |  |  | [a]_exhaust_filter_mount_x2 | Alternate | 2 |  | Optional
Exhaust_Filter (https://github.com/VoronDesign/Voron-2/blob/Voron2.4/STLs/VORON2.4/Exhaust_Filter/%5Ba%5D_filter_access_cover.stl) |  |  |  |  | [a]_filter_access_cover | Alternate | 1 |  | Optional
Exhaust_Filter (https://github.com/VoronDesign/Voron-2/blob/Voron2.4/STLs/VORON2.4/Exhaust_Filter/exhaust_filter_grill.stl) |  |  |  |  | exhaust_filter_grill | Primary | 1 |  | Optional
Exhaust_Filter (https://github.com/VoronDesign/Voron-2/blob/Voron2.4/STLs/VORON2.4/Exhaust_Filter/exhaust_filter_housing.stl) |  |  |  |  | exhaust_filter_housing | Primary | 1 |  | Optional
Gantry (https://github.com/VoronDesign/Voron-2/blob/Voron2.4/STLs/VORON2.4/Gantry/AB_Drive_Units/%5Ba%5D_cable_cover.stl) | AB_Drive_Units |  |  |  | [a]_cable_cover | Alternate | 1 | Included
Gantry (https://github.com/VoronDesign/Voron-2/blob/Voron2.4/STLs/VORON2.4/Gantry/AB_Drive_Units/%5Ba%5D_z_chain_retainer_bracket_x2.stl) | AB_Drive_Units |  |  |  | [a]_z_chain_retainer_bracket_x2 | Alternate | 2 | Included
Gantry (https://github.com/VoronDesign/Voron-2/blob/Voron2.4/STLs/VORON2.4/Gantry/AB_Drive_Units/a_drive_frame_lower.stl) | AB_Drive_Units |  |  |  | a_drive_frame_lower | Primary | 1 | Included
Gantry (https://github.com/VoronDesign/Voron-2/blob/Voron2.4/STLs/VORON2.4/Gantry/AB_Drive_Units/a_drive_frame_upper.stl) | AB_Drive_Units |  |  |  | a_drive_frame_upper | Primary | 1 | Included
Gantry (https://github.com/VoronDesign/Voron-2/blob/Voron2.4/STLs/VORON2.4/Gantry/AB_Drive_Units/b_drive_frame_lower.stl) | AB_Drive_Units |  |  |  | b_drive_frame_lower | Primary | 1 | Included
Gantry (https://github.com/VoronDesign/Voron-2/blob/Voron2.4/STLs/VORON2.4/Gantry/AB_Drive_Units/b_drive_frame_upper.stl) | AB_Drive_Units |  |  |  | b_drive_frame_upper | Primary | 1 | Included
Gantry (https://github.com/VoronDesign/Voron-2/blob/Voron2.4/STLs/VORON2.4/Gantry/Front_Idlers/%5Ba%5D_tensioner_left.stl) | Front_Idlers |  |  |  | [a]_tensioner_left | Alternate | 1 | Included
Gantry (https://github.com/VoronDesign/Voron-2/blob/Voron2.4/STLs/VORON2.4/Gantry/Front_Idlers/%5Ba%5D_tensioner_right.stl) | Front_Idlers |  |  |  | [a]_tensioner_right | Alternate | 1 | Included
Gantry (https://github.com/VoronDesign/Voron-2/blob/Voron2.4/STLs/VORON2.4/Gantry/Front_Idlers/front_idler_left_lower.stl) | Front_Idlers |  |  |  | front_idler_left_lower | Primary | 1 | Included
Gantry (https://github.com/VoronDesign/Voron-2/blob/Voron2.4/STLs/VORON2.4/Gantry/Front_Idlers/front_idler_left_upper.stl) | Front_Idlers |  |  |  | front_idler_left_upper | Primary | 1 | Included
Gantry (https://github.com/VoronDesign/Voron-2/blob/Voron2.4/STLs/VORON2.4/Gantry/Front_Idlers/front_idler_right_lower.stl) | Front_Idlers |  |  |  | front_idler_right_lower | Primary | 1 | Included
Gantry (https://github.com/VoronDesign/Voron-2/blob/Voron2.4/STLs/VORON2.4/Gantry/Front_Idlers/front_idler_right_upper.stl) | Front_Idlers |  |  |  | front_idler_right_upper | Primary | 1 | Included
Gantry (https://github.com/VoronDesign/Voron-2/blob/Voron2.4/STLs/VORON2.4/Gantry/X_Axis/XY_Joints/%5Ba%5D_endstop_pod_hall_effect.stl) | X_Axis | XY_Joints |  |  | [a]_endstop_pod_hall_effect | Alternate | 1 | Check Provider |  | Only one needed based on endstop type selected
Gantry (https://github.com/VoronDesign/Voron-2/blob/Voron2.4/STLs/VORON2.4/Gantry/X_Axis/XY_Joints/%5Ba%5D_endstop_pod_microswitch.stl) | X_Axis | XY_Joints |  |  | [a]_endstop_pod_microswitch | Alternate | 1 | Included
Gantry (https://github.com/VoronDesign/Voron-2/blob/Voron2.4/STLs/VORON2.4/Gantry/X_Axis/XY_Joints/%5Ba%5D_xy_joint_cable_bridge_generic.stl) | X_Axis | XY_Joints |  |  | [a]_xy_joint_cable_bridge_generic | Alternate | 1 | Included |  | Only one needed based on chain type
Gantry (https://github.com/VoronDesign/Voron-2/blob/Voron2.4/STLs/VORON2.4/Gantry/X_Axis/XY_Joints/%5Ba%5D_xy_joint_cable_bridge_igus.stl) | X_Axis | XY_Joints |  |  | [a]_xy_joint_cable_bridge_igus | Alternate | 1 | Included
Gantry (https://github.com/VoronDesign/Voron-2/blob/Voron2.4/STLs/VORON2.4/Gantry/X_Axis/XY_Joints/xy_joint_left_lower.stl) | X_Axis | XY_Joints |  |  | xy_joint_left_lower | Primary | 1 | Included
Gantry (https://github.com/VoronDesign/Voron-2/blob/Voron2.4/STLs/VORON2.4/Gantry/X_Axis/XY_Joints/xy_joint_left_upper.stl) | X_Axis | XY_Joints |  |  | xy_joint_left_upper | Primary | 1 | Included
Gantry (https://github.com/VoronDesign/Voron-2/blob/Voron2.4/STLs/VORON2.4/Gantry/X_Axis/XY_Joints/xy_joint_right_lower.stl) | X_Axis | XY_Joints |  |  | xy_joint_right_lower | Primary | 1 | Included
Gantry (https://github.com/VoronDesign/Voron-2/blob/Voron2.4/STLs/VORON2.4/Gantry/X_Axis/XY_Joints/xy_joint_right_upper.stl) | X_Axis | XY_Joints |  |  | xy_joint_right_upper | Primary | 1 | Included
Gantry (https://github.com/VoronDesign/Voron-2/blob/Voron2.4/STLs/VORON2.4/Gantry/X_Axis/X_Carriage/Bowden/bowden_module_front.stl) | X_Axis | X_Carriage | Bowden |  | bowden_module_front | Primary | 1 |  | Optional
Gantry (https://github.com/VoronDesign/Voron-2/blob/Voron2.4/STLs/VORON2.4/Gantry/X_Axis/X_Carriage/Bowden/bowden_module_rear_generic.stl) | X_Axis | X_Carriage | Bowden |  | bowden_module_rear_generic | Primary | 1 |  | Optional | Only one needed based on chain type
Gantry (https://github.com/VoronDesign/Voron-2/blob/Voron2.4/STLs/VORON2.4/Gantry/X_Axis/X_Carriage/Bowden/bowden_module_rear_igus.stl) | X_Axis | X_Carriage | Bowden |  | bowden_module_rear_igus | Primary | 1 |  | Optional
Gantry (https://github.com/VoronDesign/Voron-2/blob/Voron2.4/STLs/VORON2.4/Gantry/X_Axis/X_Carriage/Bowden/bsp_adapter.stl) | X_Axis | X_Carriage | Bowden |  | bsp_adapter | Primary | 1 |  | Optional
Gantry (https://github.com/VoronDesign/Voron-2/blob/Voron2.4/STLs/VORON2.4/Gantry/X_Axis/X_Carriage/Bowden/tl_collet_adapter.stl) | X_Axis | X_Carriage | Bowden |  | tl_collet_adapter | Primary | 1 |  | Optional
Gantry (https://github.com/VoronDesign/Voron-2/blob/Voron2.4/STLs/VORON2.4/Gantry/X_Axis/X_Carriage/Direct_Feed/%5Ba%5D_connector_cover.stl) | X_Axis | X_Carriage | Direct_Feed |  | [a]_connector_cover | Alternate | 1 | Included
Gantry (https://github.com/VoronDesign/Voron-2/blob/Voron2.4/STLs/VORON2.4/Gantry/X_Axis/X_Carriage/Direct_Feed/%5Ba%5D_guidler.stl) | X_Axis | X_Carriage | Direct_Feed |  | [a]_guidler | Alternate | 1 | Included
Gantry (https://github.com/VoronDesign/Voron-2/blob/Voron2.4/STLs/VORON2.4/Gantry/X_Axis/X_Carriage/Direct_Feed/%5Ba%5D_latch.stl) | X_Axis | X_Carriage | Direct_Feed |  | [a]_latch | Alternate | 1 | Included
Gantry (https://github.com/VoronDesign/Voron-2/blob/Voron2.4/STLs/VORON2.4/Gantry/X_Axis/X_Carriage/Direct_Feed/chain_anchor_generic.stl) | X_Axis | X_Carriage | Direct_Feed |  | chain_anchor_generic | Primary | 1 | Included |  | Only one needed based on chain type
Gantry (https://github.com/VoronDesign/Voron-2/blob/Voron2.4/STLs/VORON2.4/Gantry/X_Axis/X_Carriage/Direct_Feed/chain_anchor_igus.stl) | X_Axis | X_Carriage | Direct_Feed |  | chain_anchor_igus | Primary | 1 | Included
Gantry (https://github.com/VoronDesign/Voron-2/blob/Voron2.4/STLs/VORON2.4/Gantry/X_Axis/X_Carriage/Direct_Feed/extruder_body.stl) | X_Axis | X_Carriage | Direct_Feed |  | extruder_body | Primary | 1 | Included
Gantry (https://github.com/VoronDesign/Voron-2/blob/Voron2.4/STLs/VORON2.4/Gantry/X_Axis/X_Carriage/Direct_Feed/extruder_motor_plate.stl) | X_Axis | X_Carriage | Direct_Feed |  | extruder_motor_plate | Primary | 1 | Included
Gantry (https://github.com/VoronDesign/Voron-2/blob/Voron2.4/STLs/VORON2.4/Gantry/X_Axis/X_Carriage/Direct_Feed/latch_shuttle.stl) | X_Axis | X_Carriage | Direct_Feed |  | latch_shuttle | Primary | 1 | Included
Gantry (https://github.com/VoronDesign/Voron-2/blob/Voron2.4/STLs/VORON2.4/Gantry/X_Axis/X_Carriage/Printheads/E3D_V6/printhead_front_e3dv6.stl) | X_Axis | X_Carriage | Printheads | E3D_V6 | printhead_front_e3dv6 | Primary | 1 | Included - Choose one hot end
Gantry (https://github.com/VoronDesign/Voron-2/blob/Voron2.4/STLs/VORON2.4/Gantry/X_Axis/X_Carriage/Printheads/E3D_V6/printhead_rear_e3dv6.stl) | X_Axis | X_Carriage | Printheads | E3D_V6 | printhead_rear_e3dv6 | Primary | 1
Gantry (https://github.com/VoronDesign/Voron-2/blob/Voron2.4/STLs/VORON2.4/Gantry/X_Axis/X_Carriage/Printheads/TriangleLab_Dragon/printhead_front_dragon.stl) | X_Axis | X_Carriage | Printheads | TriangleLab_Dragon | printhead_front_dragon | Primary | 1
Gantry (https://github.com/VoronDesign/Voron-2/blob/Voron2.4/STLs/VORON2.4/Gantry/X_Axis/X_Carriage/Printheads/TriangleLab_Dragon/printhead_rear_dragon.stl) | X_Axis | X_Carriage | Printheads | TriangleLab_Dragon | printhead_rear_dragon | Primary | 1
Gantry (https://github.com/VoronDesign/Voron-2/blob/Voron2.4/STLs/VORON2.4/Gantry/X_Axis/X_Carriage/Printheads/Slice_Mosquito/printhead_front_mosquito.stl) | X_Axis | X_Carriage | Printheads | Slice_Mosquito | printhead_front_mosquito | Primary | 1 |  | Not Supported | PIF no longer supports Slice products
Gantry (https://github.com/VoronDesign/Voron-2/blob/Voron2.4/STLs/VORON2.4/Gantry/X_Axis/X_Carriage/Printheads/Slice_Mosquito/printhead_rear_mosquito.stl) | X_Axis | X_Carriage | Printheads | Slice_Mosquito | printhead_rear_mosquito | Primary | 1
Gantry (https://github.com/VoronDesign/Voron-2/blob/Voron2.4/STLs/VORON2.4/Gantry/X_Axis/X_Carriage/%5Ba%5D_belt_clamp_x2.stl) | X_Axis | X_Carriage |  |  | [a]_belt_clamp_x2 | Alternate | 2 | Included
Gantry (https://github.com/VoronDesign/Voron-2/blob/Voron2.4/STLs/VORON2.4/Gantry/X_Axis/X_Carriage/%5Ba%5D_blower_housing_front.stl) | X_Axis | X_Carriage |  |  | [a]_blower_housing_front | Alternate | 1 | Included
Gantry (https://github.com/VoronDesign/Voron-2/blob/Voron2.4/STLs/VORON2.4/Gantry/X_Axis/X_Carriage/blower_housing_rear.stl) | X_Axis | X_Carriage |  |  | blower_housing_rear | Primary | 1 | Included
Gantry (https://github.com/VoronDesign/Voron-2/blob/Voron2.4/STLs/VORON2.4/Gantry/X_Axis/X_Carriage/hotend_fan_mount.stl) | X_Axis | X_Carriage |  |  | hotend_fan_mount | Primary | 1 | Included
Gantry (https://github.com/VoronDesign/Voron-2/blob/Voron2.4/STLs/VORON2.4/Gantry/X_Axis/X_Carriage/probe_retainer_bracket.stl) | X_Axis | X_Carriage |  |  | probe_retainer_bracket | Primary | 1 | Included
Gantry (https://github.com/VoronDesign/Voron-2/blob/Voron2.4/STLs/VORON2.4/Gantry/X_Axis/X_Carriage/x_carriage_frame_left.stl) | X_Axis | X_Carriage |  |  | x_carriage_frame_left | Primary | 1 | Included
Gantry (https://github.com/VoronDesign/Voron-2/blob/Voron2.4/STLs/VORON2.4/Gantry/X_Axis/X_Carriage/x_carriage_frame_right.stl) | X_Axis | X_Carriage |  |  | x_carriage_frame_right | Primary | 1 | Included
Gantry (https://github.com/VoronDesign/Voron-2/blob/Voron2.4/STLs/VORON2.4/Gantry/X_Axis/X_Carriage/x_carriage_pivot_block.stl) | X_Axis | X_Carriage |  |  | x_carriage_pivot_block | Primary | 1 | Included
Gantry (https://github.com/VoronDesign/Voron-2/blob/Voron2.4/STLs/VORON2.4/Gantry/Z_Joints/z_joint_lower_x4.stl) | Z_Joints |  |  |  | z_joint_lower_x4 | Primary | 4 | Included
Gantry (https://github.com/VoronDesign/Voron-2/blob/Voron2.4/STLs/VORON2.4/Gantry/Z_Joints/z_joint_upper_hall_effect.stl) | Z_Joints |  |  |  | z_joint_upper_hall_effect | Primary | 1 | Included |  | Only needed if using hall effect
Gantry (https://github.com/VoronDesign/Voron-2/blob/Voron2.4/STLs/VORON2.4/Gantry/Z_Joints/z_joint_upper_x4.stl) | Z_Joints |  |  |  | z_joint_upper_x4 | Primary | 4 | Included |  | 3 needed if using hall effect (one replaced by hall effect joint)
Gantry (https://github.com/VoronDesign/Voron-2/blob/Voron2.4/STLs/VORON2.4/Gantry/%5Ba%5D_z_belt_clip_lower_x4.stl) |  |  |  |  | [a]_z_belt_clip_lower_x4 | Alternate | 4 | Included
Gantry (https://github.com/VoronDesign/Voron-2/blob/Voron2.4/STLs/VORON2.4/Gantry/%5Ba%5D_z_belt_clip_upper_x4.stl) |  |  |  |  | [a]_z_belt_clip_upper_x4 | Alternate | 4 | Included
Gantry (https://github.com/VoronDesign/Voron-2/blob/Voron2.4/STLs/VORON2.4/Gantry/z_chain_bottom_anchor.stl) |  |  |  |  | z_chain_bottom_anchor | Primary | 1 | Included
Gantry (https://github.com/VoronDesign/Voron-2/blob/Voron2.4/STLs/VORON2.4/Gantry/z_chain_guide.stl) |  |  |  |  | z_chain_guide | Primary | 1 | Included
Panel_Mounting (https://github.com/VoronDesign/Voron-2/blob/Voron2.4/STLs/VORON2.4/Panel_Mounting/Front_Doors/door_hinge_x4.stl) | Front_Doors |  |  |  | door_hinge_x4 | Primary | 4 |  | Cosmetic
Panel_Mounting (https://github.com/VoronDesign/Voron-2/blob/Voron2.4/STLs/VORON2.4/Panel_Mounting/Front_Doors/handle_a_x2.stl) | Front_Doors |  |  |  | handle_a_x2 | Primary | 2 |  | Cosmetic
Panel_Mounting (https://github.com/VoronDesign/Voron-2/blob/Voron2.4/STLs/VORON2.4/Panel_Mounting/Front_Doors/handle_b_x2.stl) | Front_Doors |  |  |  | handle_b_x2 | Primary | 2 |  | Cosmetic
Panel_Mounting (https://github.com/VoronDesign/Voron-2/blob/Voron2.4/STLs/VORON2.4/Panel_Mounting/Front_Doors/latch_x2.stl) | Front_Doors |  |  |  | latch_x2 | Primary | 2 |  | Cosmetic
Panel_Mounting (https://github.com/VoronDesign/Voron-2/blob/Voron2.4/STLs/VORON2.4/Panel_Mounting/bottom_panel_clip_x4.stl) |  |  |  |  | bottom_panel_clip_x4 | Primary | 4 |  | Cosmetic
Panel_Mounting (https://github.com/VoronDesign/Voron-2/blob/Voron2.4/STLs/VORON2.4/Panel_Mounting/bottom_panel_hinge_x2.stl) |  |  |  |  | bottom_panel_hinge_x2 | Primary | 2 |  | Cosmetic
Panel_Mounting (https://github.com/VoronDesign/Voron-2/blob/Voron2.4/STLs/VORON2.4/Panel_Mounting/corner_panel_clip_3mm_x12.stl) |  |  |  |  | corner_panel_clip_3mm_x12 | Primary | 12 |  | Cosmetic | 3mm clips intended for top and sides, can be larger
Panel_Mounting (https://github.com/VoronDesign/Voron-2/blob/Voron2.4/STLs/VORON2.4/Panel_Mounting/corner_panel_clip_6mm_x4.stl) |  |  |  |  | corner_panel_clip_6mm_x4 | Primary | 4 |  | Cosmetic | 6mm clips intended for back, can be used other places
Panel_Mounting (https://github.com/VoronDesign/Voron-2/blob/Voron2.4/STLs/VORON2.4/Panel_Mounting/midspan_panel_clip_3mm_x12.stl) |  |  |  |  | midspan_panel_clip_3mm_x12 | Primary | 12 |  | Cosmetic | 3mm clips intended for top and sides, can be larger
Panel_Mounting (https://github.com/VoronDesign/Voron-2/blob/Voron2.4/STLs/VORON2.4/Panel_Mounting/midspan_panel_clip_6mm_x3.stl) |  |  |  |  | midspan_panel_clip_6mm_x3 | Primary | 3 |  | Cosmetic | 6mm clips intended for back, can be used other places
Panel_Mounting (https://github.com/VoronDesign/Voron-2/blob/Voron2.4/STLs/VORON2.4/Panel_Mounting/z_belt_cover_a_x2.stl) |  |  |  |  | z_belt_cover_a_x2 | Primary | 2 |  | Cosmetic
Panel_Mounting (https://github.com/VoronDesign/Voron-2/blob/Voron2.4/STLs/VORON2.4/Panel_Mounting/z_belt_cover_b_x2.stl) |  |  |  |  | z_belt_cover_b_x2 | Primary | 2 |  | Cosmetic
Skirts (https://github.com/VoronDesign/Voron-2/blob/Voron2.4/STLs/VORON2.4/Skirts/250/front_rear_skirt_a_250_x2.stl) | 250 |  |  |  | front_rear_skirt_a_250_x2 | Primary | 2 |  | Cosmetic - Select based on frame size
Skirts (https://github.com/VoronDesign/Voron-2/blob/Voron2.4/STLs/VORON2.4/Skirts/250/front_rear_skirt_b_250_x2.stl) | 250 |  |  |  | front_rear_skirt_b_250_x2 | Primary | 2
Skirts (https://github.com/VoronDesign/Voron-2/blob/Voron2.4/STLs/VORON2.4/Skirts/250/side_skirt_a_250_x2.stl) | 250 |  |  |  | side_skirt_a_250_x2 | Primary | 2
Skirts (https://github.com/VoronDesign/Voron-2/blob/Voron2.4/STLs/VORON2.4/Skirts/250/side_skirt_b_250_x2.stl) | 250 |  |  |  | side_skirt_b_250_x2 | Primary | 2
Skirts (https://github.com/VoronDesign/Voron-2/blob/Voron2.4/STLs/VORON2.4/Skirts/300/front_rear_skirt_a_300_x2.stl) | 300 |  |  |  | front_rear_skirt_a_300_x2 | Primary | 2
Skirts (https://github.com/VoronDesign/Voron-2/blob/Voron2.4/STLs/VORON2.4/Skirts/300/front_rear_skirt_b_300_x2.stl) | 300 |  |  |  | front_rear_skirt_b_300_x2 | Primary | 2
Skirts (https://github.com/VoronDesign/Voron-2/blob/Voron2.4/STLs/VORON2.4/Skirts/300/side_skirt_a_300_x2.stl) | 300 |  |  |  | side_skirt_a_300_x2 | Primary | 2
Skirts (https://github.com/VoronDesign/Voron-2/blob/Voron2.4/STLs/VORON2.4/Skirts/300/side_skirt_b_300_x2.stl) | 300 |  |  |  | side_skirt_b_300_x2 | Primary | 2
Skirts (https://github.com/VoronDesign/Voron-2/blob/Voron2.4/STLs/VORON2.4/Skirts/350/front_rear_skirt_a_350_x2.stl) | 350 |  |  |  | front_rear_skirt_a_350_x2 | Primary | 2
Skirts (https://github.com/VoronDesign/Voron-2/blob/Voron2.4/STLs/VORON2.4/Skirts/350/front_rear_skirt_b_350_x2.stl) | 350 |  |  |  | front_rear_skirt_b_350_x2 | Primary | 2
Skirts (https://github.com/VoronDesign/Voron-2/blob/Voron2.4/STLs/VORON2.4/Skirts/350/side_skirt_a_350_x2.stl) | 350 |  |  |  | side_skirt_a_350_x2 | Primary | 2
Skirts (https://github.com/VoronDesign/Voron-2/blob/Voron2.4/STLs/VORON2.4/Skirts/350/side_skirt_b_350_x2.stl) | 350 |  |  |  | side_skirt_b_350_x2 | Primary | 2
Skirts (https://github.com/VoronDesign/Voron-2/blob/Voron2.4/STLs/VORON2.4/Skirts/%5Ba%5D_60mm_fan_blank_insert_x2.stl) |  |  |  |  | [a]_60mm_fan_blank_insert_x2 | Alternate | 2 |  | Cosmetic
Skirts (https://github.com/VoronDesign/Voron-2/blob/Voron2.4/STLs/VORON2.4/Skirts/%5Ba%5D_belt_guard_a_x2.stl) |  |  |  |  | [a]_belt_guard_a_x2 | Alternate | 2 |  | Cosmetic
Skirts (https://github.com/VoronDesign/Voron-2/blob/Voron2.4/STLs/VORON2.4/Skirts/%5Ba%5D_belt_guard_b_x2.stl) |  |  |  |  | [a]_belt_guard_b_x2 | Alternate | 2 |  | Cosmetic
Skirts (https://github.com/VoronDesign/Voron-2/blob/Voron2.4/STLs/VORON2.4/Skirts/side_fan_support_x2.stl) |  |  |  |  | side_fan_support_x2 | Primary | 2 |  | Cosmetic
Spool_Management (https://github.com/VoronDesign/Voron-2/blob/Voron2.4/STLs/VORON2.4/Spool_Management/bowen_retainer.stl) |  |  |  |  | bowen_retainer | Primary | 1 | Included
Spool_Management (https://github.com/VoronDesign/Voron-2/blob/Voron2.4/STLs/VORON2.4/Spool_Management/spool_holder.stl) |  |  |  |  | spool_holder | Primary | 1 | Included
Tools (https://github.com/VoronDesign/Voron-2/blob/Voron2.4/STLs/VORON2.4/Tools/bed_hole_marking_template_x1_Rev2.stl) |  |  |  |  | bed_hole_marking_template_x1_Rev2 | Primary | 1 |  | Optional | Not needed if buying a pre-drilled bed
Tools (https://github.com/VoronDesign/Voron-2/blob/Voron2.4/STLs/VORON2.4/Tools/rail_installation_guide_center_x2.stl) |  |  |  |  | rail_installation_guide_center_x2 | Primary | 2 | Included
Z_Drive (https://github.com/VoronDesign/Voron-2/blob/Voron2.4/STLs/VORON2.4/Z_Drive/%5Ba%5D_belt_tensioner_a_x2.stl) |  |  |  |  | [a]_belt_tensioner_a_x2 | Alternate | 2 | Included
Z_Drive (https://github.com/VoronDesign/Voron-2/blob/Voron2.4/STLs/VORON2.4/Z_Drive/%5Ba%5D_belt_tensioner_b_x2.stl) |  |  |  |  | [a]_belt_tensioner_b_x2 | Alternate | 2 | Included
Z_Drive (https://github.com/VoronDesign/Voron-2/blob/Voron2.4/STLs/VORON2.4/Z_Drive/%5Ba%5D_stopgap_80T_hubbed_gear.stl) |  |  |  |  | [a]_stopgap_80T_hubbed_gear | Alternate | 1 |  | Optional | Deprecated as aluminum 80T are readily available
Z_Drive (https://github.com/VoronDesign/Voron-2/blob/Voron2.4/STLs/VORON2.4/Z_Drive/%5Ba%5D_z_drive_baseplate_a_x2.stl) |  |  |  |  | [a]_z_drive_baseplate_a_x2 | Alternate | 2 | Included
Z_Drive (https://github.com/VoronDesign/Voron-2/blob/Voron2.4/STLs/VORON2.4/Z_Drive/%5Ba%5D_z_drive_baseplate_b_x2.stl) |  |  |  |  | [a]_z_drive_baseplate_b_x2 | Alternate | 2 | Included
Z_Drive (https://github.com/VoronDesign/Voron-2/blob/Voron2.4/STLs/VORON2.4/Z_Drive/z_drive_main_a_x2.stl) |  |  |  |  | z_drive_main_a_x2 | Primary | 2 | Included
Z_Drive (https://github.com/VoronDesign/Voron-2/blob/Voron2.4/STLs/VORON2.4/Z_Drive/z_drive_main_b_x2.stl) |  |  |  |  | z_drive_main_b_x2 | Primary | 2 | Included
Z_Drive (https://github.com/VoronDesign/Voron-2/blob/Voron2.4/STLs/VORON2.4/Z_Drive/z_drive_retainer_a_x2.stl) |  |  |  |  | z_drive_retainer_a_x2 | Primary | 2 | Included
Z_Drive (https://github.com/VoronDesign/Voron-2/blob/Voron2.4/STLs/VORON2.4/Z_Drive/z_drive_retainer_b_x2.stl) |  |  |  |  | z_drive_retainer_b_x2 | Primary | 2 | Included
Z_Drive (https://github.com/VoronDesign/Voron-2/blob/Voron2.4/STLs/VORON2.4/Z_Drive/z_motor_mount_a_x2.stl) |  |  |  |  | z_motor_mount_a_x2 | Primary | 2 | Included
Z_Drive (https://github.com/VoronDesign/Voron-2/blob/Voron2.4/STLs/VORON2.4/Z_Drive/z_motor_mount_b_x2.stl) |  |  |  |  | z_motor_mount_b_x2 | Primary | 2 | Included
Z_Endstop (https://github.com/VoronDesign/Voron-2/blob/Voron2.4/STLs/VORON2.4/Z_Endstop/nozzle_probe.stl) |  |  |  |  | nozzle_probe | Primary | 1 | Included
Z_Idlers (https://github.com/VoronDesign/Voron-2/blob/Voron2.4/STLs/VORON2.4/Z_Idlers/%5Ba%5D_z_tensioner_x4_6mm.stl) |  |  |  |  | [a]_z_tensioner_x4_6mm | Alternate | 4 | Included |  | Only needed if upgrading from V2.2 or earlier that used 6mm Z
Z_Idlers (https://github.com/VoronDesign/Voron-2/blob/Voron2.4/STLs/VORON2.4/Z_Idlers/%5Ba%5D_z_tensioner_x4_9mm.stl) |  |  |  |  | [a]_z_tensioner_x4_9mm | Alternate | 4 | Included
Z_Idlers (https://github.com/VoronDesign/Voron-2/blob/Voron2.4/STLs/VORON2.4/Z_Idlers/z_tensioner_bracket_a_x2.stl) |  |  |  |  | z_tensioner_bracket_a_x2 | Primary | 2 | Included
Z_Idlers (https://github.com/VoronDesign/Voron-2/blob/Voron2.4/STLs/VORON2.4/Z_Idlers/z_tensioner_bracket_b_x2.stl) |  |  |  |  | z_tensioner_bracket_b_x2 | Primary | 2 | Included
ZipChain (https://github.com/VoronDesign/Voron-2/blob/Voron2.4/STLs/VORON2.4/ZipChain/XY/zipchain2_xy_end.stl) | XY |  |  |  | zipchain2_xy_end | Primary | 1 |  | Optional | Deprecated in favor of Chinese chains
ZipChain (https://github.com/VoronDesign/Voron-2/blob/Voron2.4/STLs/VORON2.4/ZipChain/XY/zipchain2_xy_link_a.stl) | XY |  |  |  | zipchain2_xy_link_a | Primary | 1 |  | Optional
ZipChain (https://github.com/VoronDesign/Voron-2/blob/Voron2.4/STLs/VORON2.4/ZipChain/XY/zipchain2_xy_link_b.stl) | XY |  |  |  | zipchain2_xy_link_b | Primary | 1 |  | Optional
ZipChain (https://github.com/VoronDesign/Voron-2/blob/Voron2.4/STLs/VORON2.4/ZipChain/Z/zipchain2_z_end.stl) | Z |  |  |  | zipchain2_z_end | Primary | 1 |  | Optional
ZipChain (https://github.com/VoronDesign/Voron-2/blob/Voron2.4/STLs/VORON2.4/ZipChain/Z/zipchain2_z_link_a.stl) | Z |  |  |  | zipchain2_z_link_a | Primary | 1 |  | Optional
ZipChain (https://github.com/VoronDesign/Voron-2/blob/Voron2.4/STLs/VORON2.4/ZipChain/Z/zipchain2_z_link_b.stl) | Z |  |  |  | zipchain2_z_link_b | Primary | 1 |  | Optional
ZipChain (https://github.com/VoronDesign/Voron-2/blob/Voron2.4/STLs/VORON2.4/ZipChain/Z/zipchain2_z_link_b_locking.stl) | Z |  |  |  | zipchain2_z_link_b_locking | Primary | 1 |  | Optional
Last Updated: | 2021-12-22
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

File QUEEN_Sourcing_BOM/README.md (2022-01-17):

## This is the "QUEEN" Sourcing Guide:

My Voron 2.4 3D Printer has a name "QUEEN".

This repository contains the Sourcing Guide for the Voron 2.4 QUEEN build.

# This repositoy uses LFS extension

```
I use Git for Windows with VScode to manage this repository.  I also use Git LFS extensions for all the files.

Install Git with LFS extensions: https://git-lfs.github.com/

To Download the whole repository do the following: select the "Clone or download button" and
click on "paste to clipboard" button so you can place the URL for the GitHub repository
to the clipboard. Now Open Git Bash.  Change the current working directory to the location
where you want the cloned directory.
Type git clone, and then paste the URL you copied earlier.
$ git clone https://github.com/GadgetAngel/Voron2.4_My_Build_Log.git
Press Enter to create your local clone.
Now open Window explorer to the location of local clone.
```

## This whole repository can be downloaded as one large zip file from my Google Drive at: (if downloading via LFS is giving you are hard time)

## xxxxxxxxxxxxxxxxxxxxxxxxxxxxxxxxxxxxxxxxxxxxx

## Sourcing Guide for my Voron 2.4 QUEEN build

As a starting point for this Sourcing Guide, I based my Sourcing Guide on @shammy#6484 Sourcing Guide.  I want to thank @Shammy#6484 for sharing his Sourcing_Guide with me when I needed one.

I reviewed the "generated_bom" tab, "Voron Afterburner Parts" tab, and the "Voron Optional Parts" tab in @shammy#6484's Sourcing Guide to see if any changes needed to be made.  @Shammy#6484 had a tab labeled "Voron 2.4 350" where he listed his cost per part and the quanity he purchased for his Voron 2.4 300 mm³ build.

My build is 250 mm³. So the changes you will see are due to the size difference.  I erased all his cost information and edited the items listed to buy.  I erased all his URL links so that I could enter my URL links.  Furthermore, I do not list the cost information. You can do that if you want.  My Sourcing Guide is not for me to total my cost, it is basically a way to let you know where I purchased most of my parts for the Voron 2.4 build.

Once my cost hit over $2,000 I quit keeping track of them.

The QUEEN Sourcing Guide is contained in a file called "QUEEN_Sourcing_BOM.xlsx" which is inside a .zip file called "QUEEN_Sourcing_BOM.xlsx.zip".  This makes it easier to download the Excel spreadsheet from GitHub since it is contained within a .zip file.

If I find anything missing after I publish this "QUEEN Sourcing Guide", I will update it and repost it here.

I hope this helps others who are in the middle of sourcing their Voron 2.4 DIY 3D printer.

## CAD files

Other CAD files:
The_.STL_Files/Copy_of_.STLs_forQUEEN/Skirt/Rear/Middle/plug_panel_filtered_mains_x1.stl
The_.STL_Files/Copy_of_.STLs_forQUEEN/Gantry/X_Axis/X_Carriage/MODS/Klicky_Probe_Mod_non_built-in/KlickyProbe_Dock_Side_Mount_Fixed_Main_x1.stl
The_.STL_Files/Copy_of_.STLs_forQUEEN/Gantry/X_Axis/X_Carriage/Direct_Feed_Stealthburner/[a]_stealthburner_main_body_beta3_x1.stl
The_.STL_Files/Copy_of_.STLs_forQUEEN/LitterBox_Mod/Rear__Skirt/Rear_Extended_Skirt/A_Side/Faux_Z_Belt_Drive_A/Faux_A_Z_Belt_Drive_Main_x1.stl
The_.STL_Files/Copy_of_.STLs_forQUEEN/Gantry/X_Axis/X_Carriage/MODS/Euclid_Probe Mod/Derpimus_OmronFotek90_Main_x1.stl
The_.STL_Files/Copy_of_.STLs_forQUEEN/Z_Drive/z_drive_main_a_x2.stl
The_.STL_Files/Copy_of_.STLs_forQUEEN/LitterBox_Mod/Rear__Skirt/Rear_Extended_Skirt/B_Side/Faux_Z_Belt_Drive_B/Faux_B_Z_Belt_Drive_Main_x1.stl
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

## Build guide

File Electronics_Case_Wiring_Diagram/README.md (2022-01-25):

# This repository uses LFS extension

```
I use Git for Windows with VScode to manage this repository.  I also use Git LFS extensions for all the files.

Install Git with LFS extensions: https://git-lfs.github.com/

To Download the whole repository do the following: select the "Clone or download button" and
click on "paste to clipboard" button so you can place the URL for the GitHub repository
to the clipboard. Now Open Git Bash.  Change the current working directory to the location
where you want the cloned directory.
Type git clone, and then paste the URL you copied earlier.
$ git clone https://github.com/GadgetAngel/Voron2.4_My_Build_Log.git
Press Enter to create your local clone.
Now open Window explorer to the location of local clone.
```
## This whole repository can be downloaded as one large zip file from my Google Drive at: (if downloading via LFS is giving you are hard time)

## xxxxxxxxxxxxxxxxxxxxxxxxxxxxxxxxxxxxxxxx

# Electronics Case Wiring Diagram for QUEEN (my Voron 2.4 build):

This repository contains JPG and PDF files for the electronics case for QUEEN.  I am presently working on the "Functional Wiring Diagram" for my QUEEN Build.  I am concurrently working on the "Real World" Electronics Case Diagram which will show you the actual routing of all the wires I will use for my QUEEN Build.

---

## Sourcing Guide for my QUEEN Voron 2.4 Build:

[Here is the Excel spreadsheet as a sourcing guide for my Voron 2.4](../QUEEN_Sourcing_BOM).

---

## Fusion 360 CAD files and STEP files:

I have spent 3 months creating the 3D model of my QUEEN Voron 2.4 250 mm³ build.

I have used the CAD models from each MOD (listed below) and incorporated the respective MOD's CAD model into my QUEEN Fusion 360 model.  After working in Fusion 360 for the past 3 months I have become aware of a couple of things:

1.  When exporting sub-Assemblies from Fusion 360 in .STEP format the only sub-assemblies that get put into the STEP file are the sub-assemblies that are visible at the time the exported STEP file is created.  So when you use STEP files expect all the sub-assemblies to be visible when you first open up the STEP file.  You will have to turn off the options that you do not want to see after you upload the STEP file to Fusion 360 (or your CAD software).

2. If a MOD did not have a Fusion 360 CAD model, I used the .stl files from the MOD and used Fusion 360 to convert the .stl files into parametric bodies.

3.  If you upload .f3d sub-Assembly file and all sub-assembly options are turn on, then please just turn off the sub-assemblies you do not want to see. Sometimes, I exported the .STEP files at the same time I was creating the .f3d files, so I might have left options turned on, so I could save the .STEP file.

4. I have noticed that if one uses the "save a copy as ..." option that parts will lose their position (x,y,z).  So to create the sub-assemblies I did a "copy" to the clip board and then placed the clip board contents into a new file and saved that file.

GadgetAngel's Voron 2.4 Fusion 360 CAD model (.f3d) and (.STEP) files:

The full model for QUEEN has a fusion 360 (.f3d) file and STEP file.  The STEP file for the full model has been integrated by myself from all the sub-assemblies STEP files. This way I could check the sub-assembly files to ensure that they were created correctly.

1.  [QUEEN's Voron 2.4 Fusion 360 model and STEP version](../CAD/QUEEN_Voron_2.4_Build_ZIP_files)

2.  [QUEEN's Voron 2.4 Fusion 360 subAssembly model (.f3d) and .STEP versions for the Electronics from the Bottom Electronics Case](../CAD/Electronics_forBottom_Electronic_Case/ZIP_files)

3.  [QUEEN's Voron 2.4 Fusion 360 subAssembly model (.f3d) and .STEP versions for Electronics from the LitterBox Case](./CAD/Electronics_forLitterBox_Case/ZIP_files)

4.  [QUEEN's Voron 2.4 Fusion 360 subAssembly model (.f3d) and .STEP versions for the LEDs](../CAD/LEDs/ZIP_files)

5.  [QUEEN's Voron 2.4 Fusion 360 subAssembly model (.f3d) and .STEP versions for all Panels & Clips](../CAD/Panel_Mounting/QUEENv98_SubAssmbly_Panel&Clips_ZIP_files)

6.  [QUEEN's Voron 2.4 Fusion 360 subAssembly model (.f3d) and .STEP versions for different panels, see this directory for additional sub-assemblies](../CAD/Panel_Mounting)

7. [QUEEN's Voron 2.4 Fusion 360 subAssembly model (.f3d) and .STEP versions for all Skirts](../CAD/Skirts/QUEENv98_SubAssmbly_ALL_Skirts_ZIP_files)

8. [QUEEN's Voron 2.4 Fusion 360 subAssembly model (.f3d) and .STEP versions for different Skirts (i.e., Front Skirt, Left-Side Skirt, etc.), see this directory for additional sub-assemblies](../CAD/Skirts)

9. [QUEEN's Voron 2.4 Fusion 360 subAssembly model (.f3d) and .STEP versions for all the mods located under the Heated Bed & a Filament Runout Sensor](../CAD/Under_Heated_Bed/ZIP_files)

10. [QUEEN's Voron 2.4 Fusion 360 subAssembly model (.f3d) and .STEP versions for my Z Driver Tensioner Mod](../CAD/Z_Drive/ZIP_files)

11. [QUEEN's Voron 2.4 Fusion 360 subAssembly model (.f3d) and .STEP versions for the Exhaust Filter](../CAD/Exhaust_Filter/ZIP_files)

12.  [QUEEN's Voron 2.4 Fusion 360 subAssembly model (.f3d) and .STEP versions for the Frame](../CAD/Frame/ZIP_files)

13. [QUEEN's Voron 2.4 Fusion 360 subAssembly model (.f3d) and .STEP versions for the Gantry](../CAD/Gantry/ZIP_files)

14. [QUEEN's Voron 2.4 Fusion 360 subAssembly model (.f3d) and .STEP versions for the Litter Box Mod and its sub-assemblies, see this directory for additional sub-assemblies](../CAD/Litter_Box_CAD)

15. [QUEEN's Voron 2.4 Fusion 360 subAssembly model (.f3d) and .STEP versions for the Z-Endstop called the "SexBolt Z-Endstop"](../CAD/Z_Endstop/ZIP_files)

16. [QUEEN's Voron 24 Fusion 360 subAssembly model (.f3d) and .STEP version for the BTT piTFT V2.0 articulating arm with display mount](../CAD/Skirts/Front/Middle/ZIP_files)

---

## .STL list of files needed for each MOD:

I will be publishing a folder of .stl files for all the printed parts I am using for my QUEEN build, including the ones from my PIF parts ~~(coming soon)~~.

My intent is to list the files needed in each Sub-Assembly and indicate which ".stl files" need to be replaced or exchanged for a Modded ".stl" file.  I think an [EXCEL spreadsheet would help with this task and can be found here](../The_.STL_Files/Excel_Spreadsheet_.stl_files).

The [".STL" files for my QUEEN Voron 2.4 build can be found here](../The_.STL_Files/Copy_of_.STLs_forQUEEN_As_Built_will-not-be-updated)

---

## Lesson Learned while doing the "Electronics Case Wiring Diagram" for QUEEN:

I finished the AC wiring diagram for the QUEEN build today. From doing the wiring diagram
I determined that I needed to make some adjustments in my power supplies and do more work with the 3D model layout.

I have decided to split the Wiring Diagram for my Voron 2.4 printer up into two wiring diagrams: "AC Electrical Wiring Diagram" and "DC Electrical Wiring Diagram".

The "DC Electrical Wiring Diagram" will show how to set up the Octopus Pro board and all the DC wiring not included in the "Wiring Harness Diagram" like LEDs, fans, DC light switches and so on. I will work on this one next.

The first draft of the "AC Electrical Wiring Diagram" is done and is now being published.  I still might need to make changes to it once I start working on the DC wiring diagram.  Please remember this whole repository is a "Work in progress" because I still have not finished building my Voron 2.4 printer. I have all the building material, but I want to document how I will be interconnecting all the modules before I start putting things together.

### Requirements for my Voron 2.4 printer build

One of the requirements for my Voron 2.4 printer is that I want to be able to reboot the Voron 2.4 printer without requiring a reboot of Mainsail or Fluidd (the Raspberry Pi) along with the printer's motherboard and power supplies.  To accomplish this goal, I have decided that my Raspberry Pi will always remain powered up. It can be shut down through the BIG RED mushroom button, but typically it will always be turned on while the Voron 2.4 printer may not be turned on.

I also want to use some extra features with my Voron 2.4 printer, like, filament runout sensor, filament jam detection, automatic shutdown after print job has finished, and resume 3D print after power failure.

The filament runout sensor and filament jam detection will be looked at when I do the DC wiring diagram for the electronic case (which I will be working on next).  The "automatic shutdown after print job has finished" and "resume 3D print after power failure" features needed to be looked at while doing the AC electrical wiring.

These two features have been incorporated into the AC electrical wiring diagram.  I am using BTT's relay V1.2 to perform the "automatic shutdown after print finishes" feature~~, and I am using BTT's UPS module to perform the "resume 3D print after power failure" feature.~~ I also added in another set of relays to allow the Raspberry Pi to remotely shut down the Voron 2.4 printer (along with the PSU, except for the PSU that supplies 5VDC power for the Raspberry Pi). I also have a mechanical Hour-counter and Engergy Meter incorporated in the front and side skirt of my Voron 2.4 printer that I need to control.  The Energy Meter will always be on when the Voron 2.4 printer is powered up (it is located on the right-hand side of my printer).  The mechanical Hour-Counter will only run when the Voron 2.4 printer is actually producing a 3D part and is located on the front skirt.  This way I can see the number of actual hours of print time. This Hour-Counter runs through a relay, so I can control when it is turned on.

The BTT's V1.2 are relays that are normally opened (NO) so when I added my additional relay I needed to ensure that I could configure it to be NO or NC.  The relay that controls the Hour-counter is NO type of relay.

I also want the capability to use momentary switches on the left-hand side and right-hand side of my printer to power up or down the Voron 2.4.  These momentary switches are active low and are hardwired directly into the relays so that software is not needed to control them.  I call these "hardware reboot switches".  These switches will only reboot the Voron 2.4 (not the Raspberry Pi).  The switch that is on the back of the Voron 2.4 will reboot both the Raspberry Pi and the Voron 2.4 printer.  I will also mount a "mini Red push button (momentary switch)" to one of the keyholes on the Voron 2.4 skirt which allows me to reboot the Voron 2.4 printer via the BTT's V1.2 relay modules.

Since I want the Raspberry Pi to be "alway ON", I need to buy another 5V power supply.  I decided to remove the UHP-200-12 PSU and replace that unit with a PSU that is two PSUs in one unit.  I bought a Meanwell RD-50A PSU which has a 5VDC PSU (@ 6 Amps) and 12VDC PSU (@ 2Amps) in one metal box.  Since the Stealthburner has been realeased as a beta, I have added it to my Voron 2.4 printer and ended up switching all my LEDs from 12VDC to 5VDC.  I will be using Adafruit Neopixels LEDs only, and they only work at 5 Volts.  So I downsized my 12V supply and doubled my 5V power supply.

The Meanwell RS-25-5 will be the power supply that always remains on and is attached to the external UPS [APC 1500VA UPS Battery Backup and Surge Protector, BX1500M Power Supply](https://www.amazon.com/gp/product/B06VY6FXMM) along with Voron 2.4 printer.  I am using a "BIG RED" button or mushroom button between the APC UPS unit and the power input (filtered power inlet) for the Voron 2.4 printer.  I have added this for saftey reasons.  The mushroom box assembly will have a long power cord, so I can place it where ever I want.  I also have smoke detector located above the 3D printer.

In my AC wiring diagram you will see things like "grounding straps" and "Ferrite core filters".  These are present to help reduce cross talk.

Logically I have 5 power supplies, two 5V PSU, one 12V PSU, one 24V PSU and one 48V PSU.  One PSU combines two of these into one PSU (Meanwell RD-50A combines a 5V PSU and 12V PSU into one PSU).

In the AC electrical wiring diagram some lines are thicker than the others. I did this on purpose so that you will automatically recognize the AC lines from the DC lines.  The AC lines are thicker and are distributed using UK2.5 terminal blocks (or Dinkle DK4N termainal blocks).  The DC lines are thin and use WAGO nuts for distrubution blocks.

Since the Raspberry Pi is a 3.3V logic device, I use [3.6V Zener Diodes](https://www.amazon.com/Chanzon-34-Values-Zener-Assorted/dp/B07BTWBXJ3) for overvoltage protection on the Raspberry Pi's GPIO lines when using a 5VDC power supply for the 4-channel relay module to activate the relay's coils. Even tho my AC wiring diagram shows I will be using a 4-channel relay module, I might only install a one channel relay module. The resons for going to one channel is that I do not need a 4-channel relay module and I have a one channel relay module sitting in a drawer.

Below you will find the JPG and the PDF files for the "Voron 2.4 AC Electrical Wiring Diagram".

After finding a [schematic diagram of the BTT relay V1.2 from a russian website](https://github.com/GadgetAngel/Voron2.4_My_Build_Log/blob/main/Resources/BTT%20Relay%20V1.2%20Schematic.pdf) I have become aware that I can control the PSUs with the Raspberry Pi via the BTT Relay V1.2 modules without the use of a second relay module. Therefore, the secondary relay module will only control the mechanical Hour-Counter.  I have updated my AC Electrical Wiring Diagram to reflect this change.

After a discussion in the Voron discord channel with other more experienced Voron users the following question arose: "Does the Voron 2.4 printer even have the capacity to resume print?  If the Gantry sags at all it won't, since you wouldn't be able to perform QGL with a buildplate already occupied.".  Due to this fact using the BTT UPS modules is now out since I will not be able to get the flying gantery back to where it needs to be to resume a print.  I will be removing the "resume after power failure" as a requirement for my Voron 2.4 printer.

Also, another Voron user found an error in my first AC wiring diagram. I forgot to tie all my V- (DC negative voltage) terminals together to establish a common voltage reference between different power supplies. The revised AC wiring diagram now has the V- terminals all tied together.

1/9/2022:

Ok, folks I have some explaining to do. But be aware that now I will be discussing **TWO** different Voron 2.4 printer builds in this build log.

I was watching the build of the Voron 2.4 LDO kit on [@Steve Builds](https://www.youtube.com/channel/UC8VsL6u5PiOgy6n4I4b4Ufw) and have been very impressed with the LDO kit.  So after discussng my options with my husband we decided that the best route forward for me is to buy the LDO kit and build the LDO 300 mm³ build.  I'm still planning on building the 250 mm³ QUEEN build but to build QUEEN I need a work horse 3D printer that prints ABS really well.

Now you are thinking that is nuts. Not really! I added up the cost of just getting the 3D printed parts done by a commerical vendor and the cost is over $5,000.  So the cost of the LDO kit is only $1,350. So instead of paying someone else to print the QUEEN ABS parts I will get a new Voron 2.4 LDO 300 mm³ Build which I will call "Voron_LDO" and print the ABS parts for QUEEN myself on the Voron_LDO printer.  This way I get more experience with the printer profiles. I will also be able to print the modified parts and test them out.

I will also have another printer that I can modifiy once the QUEEN build is finished.

Furthermore, I like to think of this rationalization as a way to bootstrap my Voron printer experience.  Wink Wink.

1/11/2022:

I am still working on the DC wiring Diagram for the QUEEN build.  Here is what I am trying to figure out right now.

I have bought a [ERCF v1.1 moster kit - 6 chart version](https://deepfriedhero.in/products/enraged-rabbit-carrot-feeder-v1-1-monster-kit?variant=41260783534249) because I will someday print out the parts and put it together to do multi-material printing.

When planning the QUEEN build I want to ensure that the parts I use for the X-Axis and the toolhead will accomodate the ERCF v1.1. The ERCF adds on additional equipment that the "ERCF Easy Board" will handle. The ["ERCF Easy Board"](https://deepfriedhero.in/products/ercf-ez-board) can be setup in Klipper as an additional MCU and that way the board's PIN definitions can be used.

The reason I choose the [Hartk's ERCF v.3 toolhead board](https://deepfriedhero.in/products/voron-afterburner-toolhead-board-v3-rabbit) is that I knew I already purchase the ERCF V1.1 monster kit.

So now that I provided the background story, what am I confused about? Well, after reading the manual for the ["ERCF Easy Board"](https://deepfriedhero.in/products/ercf-ez-board) I learned that I have the following connections available:

On the [ERCF Easy Board, page 93, I see](http://nbviewer.jupyter.org/github/EtteGit/EnragedRabbitProject/blob/main/Documentation/ERCF_Manual.pdf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):

    1.  "Servo";
    2.  "Selector Motor";
    3.  "Gear Motor";

On the [ERCF Easy Board, page 94, I see](http://nbviewer.jupyter.org/github/EtteGit/EnragedRabbitProject/blob/main/Documentation/ERCF_Manual.pdf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):

    4.  "Selector Endstop";
    5.  "Encoder";

Besides the ERCF prep for the QUEEN build, I also want to prep QUEEN for the Voron Stealthburner fan assembly.  To use the LEDs on the Stealthburner we need a Data PIN on the Hartk's ERCF v.3 toolhead board along with GND and 5VDC to power the Neopixel LEDs. The [Hartk's ERCF v.3 toolhead board](https://deepfriedhero.in/products/voron-afterburner-toolhead-board-v3-rabbit) will work only if you are running stock endstop pod, and you need to run [Klicky_Probe](https://github.com/jlas1/Klicky-Probe) (which we are).  Therefore, @Hartk1213 says that the following, hookup should be used:

```
Klicky --- XES header
Filament Sensor --- probe header (those can run on 24v)
LEDs --- FS header (5v, S, G)
```

Hartk1213 says ``that should get you ERCF , LEDs and Klicky all at the same time``.

Ok, but if the ["ERCF Easy Board"](https://deepfriedhero.in/products/ercf-ez-board) has the connection for the .....thinking....
I see now, the "Filament Sensor" is the "AH3364Q-P-B Hall effect sensor that is built into the toolhead". Look at [ERCF Easy Board,page 80](http://nbviewer.jupyter.org/github/EtteGit/EnragedRabbitProject/blob/main/Documentation/ERCF_Manual.pdf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)

I plan on using the Bondtech LGX extruder instead of the clockwork1 (CW1) extruder. So I think from typing this all out I now understand how the connections all work.

I need to ensure that for the QUEEN build the correct LGX part is being used. It has to be the 3D part from the ERCF projocet, so I can install the [AH3364Q-P-B Hall effect sensor](https://www.diodes.com/assets/Datasheets/AH3364Q.pdf) and run it at 24VDC.

1. Then I can use the "ABL Header" on the [Hartk's ERCF v.3 toolhead board](https://deepfriedhero.in/products/voron-afterburner-toolhead-board-v3-rabbit) to connect up the "AH3364Q-P-B Hall effect sensor" which is built-in to the [LGX_on_AfterBurner_Adapter_ERCF_Sensor.stl](https://github.com/EtteGit/EnragedRabbitProject/blob/main/Filament_Sensor/Stls/LGX/LGX_on_AfterBurner_Adapter_ERCF_Sensor.stl) 3D printed part.

BTW, I renamed the file to "LGX_on_AfterBurner_Adapter_ERCF_Sensor_fromERCFproj.stl".

2.  Ensure the [Klicky_Probe](https://github.com/jlas1/Klicky-Probe) is connected to [Hartk's ERCF v.3 toolhead board's](https://deepfriedhero.in/products/voron-afterburner-toolhead-board-v3-rabbit) "XES" header.

3.  Connect the Neopixel LEDs for the Stealthburner fan assembly to [Hartk's ERCF v.3 toolhead board's](https://deepfriedhero.in/products/voron-afterburner-toolhead-board-v3-rabbit) "FS" connector.

And

4.  I connect "Servo", "Selector Motor", "Gear Motor", "Selector Endstop" and "Encoder", not to the Octopus Pro board, but to the ["ERCF Easy Board"](https://deepfriedhero.in/products/ercf-ez-board) which uses a "Seeeduino XIAO" processor which talks to the Raspberry Pi 4B board via USB connection (USB-C on Seeeduino XIAO to USB-2.0 on the Raspberry Pi).

The Seeeduino XIAO microcontroller and sensors are powered through the USB-C cable from the RaspberryPi USB port while the stepper motor drivers are powered by the ERCF Easy Board's PSU (12/24V) on-board connector.

So all the connection on the ERCF Easy Board will send data to the rapberry pi via USB.

#### The only connections to the Octopus Pro board we need to make are the following:

1.   Klicky_Probe connected to the "XES" connector of the ERCF v.3 toolhead board to the "STOP_7" endstop connector of the Octopus Pro board (on the LDO Kit they refer to this as the "Z Probe" line).

2.  Built-in "(AH3364Q-P-B) Hall effect sensor" for the LGX_ERCF part connected to the "ABL" connector of the ERCF v.3 toolhead board to the "Probe" connector on the Octopus Pro board with the "Probe Voltage Select" header's Jumper {on the Octopus Pro board} set on the pins that select 24VDC (or the Board's Vᵢₙ).

    * Also, on the Octopus Pro board ensure the Jumper on the "Probe Type Select" header is **REMOVED** so that PNP type is used for the "Probe" connector.  The datasheet on the "AH3364Q-P-B Hall effect sensor" states the following:

```
The single open drain output can be switched on with South pole of
sufficient strength. When the magnetic flux density (B) perpendicular
to the package is larger than the operate point (BOP) the output is
switched on (pulled low) and is held on until magnetic flux density B is
lower than the release point (BRP). The output remains switched off
for North pole fields to or no magnetic fields.
```

This statement indicates to me that the "AH3364Q-P-B Hall effect sensor" works like a "PNP" type Probe. For information on how "PNP" and "NPN" see https://automation-insights.blog/2018/02/14/an-easy-way-to-remember-pnp-and-npn-sensor-wiring/.

3.  Neopixels should have an in-line 300 to 500 Ohm resistor between the RGB header's data output pin and the input to the first NeoPixel. The resistor should be at the end of the wire closest to the NeoPixel(s), not the Octopus Pro board.

Neopixels with an in-line 300 to 500 Ohm resistor attached to the first Neopixel which is then attached to the other two Neopixels in the Stealthburner fan assembly. These Stealthburner NeoPixels get connected to the "FS" connector of the ERCF v.3 toolhead board which then goes to the ~~"DRIVER_7" stepper motor socket~~ RGB header of the Octopus Pro board.

From reading about NeoPixels today and Adafruit's best-practices in using NeoPixels (https://learn.adafruit.com/adafruit-neopixel-uberguide/best-practices), I quote Adafruit:

```
Try to minimize the distance between the controller board and first pixel, so the signal is clear.
A meter or two is usually no problem. Much longer and things can become unreliable. Individual NeoPixels can act as repeaters for long runs.
```

On a Voron 2.4 the distance from the motherboard to the toolhead is over 2 meters which is above Adafruit's recommendation.
So to accomodate this limitation one could place a single NeoPiexel halfway down the wiring harness to the toolhead so that it acts as a repeater.

On second thought, I want to have more than one strip of NeoPixels.  I will have the individual NeoPixels for the Stealthburner, but I plan on using NeoPixel stips on the sids panel and up in the top of the heated chamber. I also plan on putting a string underneath the printer (lights in the electronics compartment and in the litter box compartment).  Since each Neopixel has its own address, I can use one data line for all these lights.

So with all these Neopixels strings I will have plenty of NeoPixel repeaters in my Voron 2.4 printer QUEEN build. That will not be the case for my Voron 2.4 LDO build.

If for your build, you only want to attach the "Voron Stealthburner" Neopixel LEDs, than I would buy a couple extra single Neopixels LEDs and place them in the wiring harness at which ever location you want to act as a repeater for the Neopixel's on the toolhead (one extra single NeoPixel placed halfway down the wiring harness will do the trick).  This way the data line will be boasted, and its signal level will not degrade so that the next Neopixel can correctly interpret the previous Neopixel's data transmission.

The "FS" connector comming from the ERCF v.3 toolhead board has one wire that needs to be connected up on the Octopus Pro board (Data line for the Neopixel LED which will be using a 5 Volt logic level {not a 3.3 Volt logic level})

~~But first we must properly configure the "DRIVER_7" stepper motor socket.  Ensure that "DRIVER_7" mode Jumpers are set for UART mode if the rest of the stepper motor driver sockets are configured for SPI mode.  So if you are using the TMC5160_PRO drivers then "DRIVER_0", "DRIVER_1", "DRIVER_2", "DRIVER_3", "DRIVER_4", "DRIVER_5", and "DRIVER_6" will all be configured for SPI mode.~~

~~So set the "DRIVER_7" for UART mode. By configuring the opposite mode for the empty driver socket you are ensuring that the empty driver socket will not interfear with the communication bus of the other 7 driver sockets.~~

~~If you look at the schematic diagram for the Octopus Pro you will see that "DRIVER_7" has a chip select line called "DRIVER7_CS":~~ The Picture below went with the crossed out text, so please ignore it.
 DRIVER7_Schematic_Diagram

~~If you follow the "DRIVER7_CS" line you will see it leads you to a device labeled ["TXS0104EPWR"](https://github.com/GadgetAngel/Voron2.4_My_Build_Log/blob/main/Resources/TXS0104E%204-Bit%20Bidirectional%20Voltage-Level%20Translator_txs0104e.pdf)~~:
The Picture below went with the crossed out text, so please ignore it.
DRIVER7_Shiftleveler_to_5Vlogic

~~This "TXS0104EPWR" shifts the DRIVER7_CS signal line from 3.3VDC logic level to 5VDC logic level. Which is what we want for the LEDs data line for the stealthburner fan assembly.~~

~~You might be asking why do you not just use the Octopus Pro RGB header? Well you could. But since the Stealthburner uses Neopixels LEDs, I decided to use Neopixels throughout the QUEEN build. Remember that is why I bought in a second 5V PSU.  So to control the other lights with the Octopus Pro board I will need more than one Neopixel Data line.  I just choose to use the DRIVER7_CS line for the stealthburner LEDs because when I am ready to do the other Neopixels I will use the RGB header or the DRIVER7_STEP or the DRIVER7_DIR lines.~~

Since I have learned more about NeoPixels I will be following [Adafruit's recommendations on how to hook up Neopixels](https://learn.adafruit.com/adafruit-neopixel-uberguide/best-practices).

Like I said earlier, The "FS" connector comming from the ERCF v.3 toolhead board has one wire that needs to be connected up to the Octopus Pro board (the NeoPixel's Data line).  As I already stated, I will be using an in-line 300 to 500 Ohm resistor between the RGB header's data output pin and the input to the first NeoPixel.

**Please**, **Please**, put the resistor in-line with the first NeoPixel on the data line before trying to hook up power to the NeoPixels.  If you do not, you could permentaly damage the first NeoPixel and have to rewire the Stealthburner to fix the NeoPixel.

Since I am using an independent external power supply to power my NeoPixel strips (I am not using the Octopus Pro to power the LEDs) I will be placing a large capacitor (500–1000 µF at 6.3 Volts or higher) across the + and – 5VDC terminals of the Meanwell RD-50A PSU.  This is what Adafruit remcommends doing, I qoute them below:

```
Before connecting a NeoPixel strip to ANY source of power, a large capacitor (500–1000 µF at 6.3 Volts or higher) across the + and – terminals provides a small power reservoir for abrupt changes in brightness that the power source might not otherwise handle — a common source of NeoPixel “glitching.” The capacitor also buffers sudden changes in the current drawn by the strip.
```

~~Please, remember to hook up the 5VDC line from the ERCF v.3 toolhead board to the 5V line on the DRIVER7 red socket.  If you do not want to use a Dupont connector for the 5VDC line then use a JST connector and attach it to "STOP_3" connector of Octopus Pro board.~~

Please remember to hook up the 5VDC line from the Meanwell RD-50A PSU to the first NeoPixel 5V DC pad and use "Common V- Ground" (the common ground reference between all the PSU in the build) to the GND pad on the first NeoPixel.

Note: You only need **one** 300 to 500 Ohm resistor between the RGB header's data output pin and the first NeoPixel.  So in my case since I have many NeoPixel LEDs I will do this only to the first NeoPixel that will be located in the bottom electronics case for the QUEEN build.

But for my Voron_LDO build, I will only be placing the Neopixels on the "Voron Stealthburner".  In this case I will probably power the NeoPixels from the Octopus board.  I will buy four (4) individual NeoPixel LEDs for my Voron Stealthburner (in fact I already have them).  I will buy two extra in case I screw up on the soldering and ripe a pad off of one of the NeoPixels boards.  Furthermore, I will place one of the "extra" Neopixels halfway down my wiring harness to act as a repeater for the Stealthburner's first Neopixel. So I will place an in-line 300 to 500 Ohm resistor between the (Octopus board) RGB header's data output pin and the "extra" Neopixel.  Remember this in-line resitor must be placed closer to the Neopixel than the RBG header. Since I am **NOT using an independent PSU to power the NeoPixels for my Voron_LDO build**, I **do not need to use** the large capacitor (500–1000 µF at 6.3 Volts or higher) across the + and – terminals of my PSU.

I hope this procedure is clear.  Again, please place an in-line 300 to 500 Ohm resistor between the (Octopus board) RGB header's data output pin and the first Neopixel board.  You will not damage anything by doing this and in fact you could save the Neopixel board from being damaged.

4.  Now we need to connect the extruder motor up to the Octopus Pro.  The LGX extruder motor will connect to the "E-STEP" connector of the ERCF v.3 toolhead board which then connects to "MOTOR6" connector of the Octopus Pro board.

5.  The "CT" or "Chamber Thermistor" line of the ERCF v.3 toolhead board will connect to the "T1" on the Octopus Pro board.

6.  The "TH0" or "Hotend Thermistor" line of the ERCF v.3 toolhead board will connect to the "T0" on the Octopus Pro board.

7.  The "PCF" or "Parts/Print Cooling Fan" line of the ERCF v.3 toolhead board will connect to the "FAN0" on the Octopus Pro board.

8.  The "HEF" or "Hot-End Fan" line of the ERCF v.3 toolhead board will connect to the "FAN1" on the Octopus Pro board.

9.  The "HE0" or "Hot-End Heater" line of the ERCF v.3 toolhead board will connect to the "HE0" or "HEAT0" on the Octopus Pro board.

10. The "24VDC" line of the ERCF v.3 toolhead board will connect to the "BED POWER IN" on the Octopus Pro board.

11. The "AGND" line of the ERCF v.3 toolhead board will connect to the GND PIN on the Octopus Pro board's "T3" connector.

12.  The "GND" line of the ERCF v.3 toolhead board will connect to the "Voron 2.4 AC Wiring Diagram"'s "Common V- Ground" reference (the point where you attach all the V- terminal of each PSU you have in the Build).

So, thank you for letting me type and figure out how this all connects up.  That is how you connect up the Hartk's ERCF v.3 toolhead board to the Octopus Pro if you are using Stealthburner fan assembly on the LGX extruder with Neopixels, Klicky_Probe (XES), HEF, HE0, TH0, Chamber Thermistor(CT), PCF, HEF, LGX motor, 5VDC, 24VDC, GND, Analogue GND (AGND) and "Common V-" from all the PSUs (GND).

Next we need to connect up all the motors and endstops:

13. The "X" line of the [Voron 2.4 XY Microswitch Endstop PCB board](https://deepfriedhero.in/products/voron-2-4-xy-microswitch-endstop-pcb) will connect to the "STOP_0" on the Octopus Pro board.

14. The "Y" line of the [Voron 2.4 XY Microswitch Endstop PCB board](https://deepfriedhero.in/products/voron-2-4-xy-microswitch-endstop-pcb) will connect to the "STOP_1" on the Octopus Pro board.

15. The "HE1" line of the [Z Endstop PCB for Voron v2.4 board](https://deepfriedhero.in/products/z-endstop-pcb-for-voron-v2-4) (on the LDO Kit they refer to this as the "Nozzle Probe" line) will connect to the "STOP_2" on the Octopus Pro board.

Motor cables: Please use a LED light to ensure that the pairs of wires for each motor coil are lying next to each other in the motor cable's connector. If the two adjacent wires do not turn on the LED light when you turn the shaft of the motor then you will need to find the appropriate pair of wires and ensure that they are adjacent to each other in the JST connector.  What do I mean by two adjacent wires? Well the JST connector has 4 pins. Pick a starting point, call that "PIN 1" then the next pin adjacent to it in the JST connector is "PIN 2". Place an LED across "PIN 1" and "PIN 2". Turn the stepper motor shaft to see if the LED turns on while you turning the motor's shaft. If the LED turns on then "PIN 1" and "PIN 2" are a coil pair. Now check "PIN 3" and "PIN 4", just to ensure that the second motor coil is working properly. Place the LED across "PIN 3" and "PIN 4", does the LED turn on? Now that you have determined which pairs of wires make up the motor's coils. Place the coil pairs as follows: PIN1 and PIN2 are a coil pair, PIN3 and PIN4 are a coil pair.

16. "A" Motor cable is the motor located in the "Rear Right of Gantry" as if standing in front of an upright printer and looking towards it. Place the "A" Motor cable into "Motor_1" connector on the Octopus Pro board.

17. "B" Motor cable is the motor located in the "Rear Left of Gantry" as if standing in front of an upright printer and looking towards it. Place the "A" Motor cable into "Motor_0" connector on the Octopus Pro board.

18. "Z0" Motor cable is the motor located in the "Front Left" as if standing in front of an upright printer and looking towards it. Place the "A" Motor cable into "Motor_2" connector on the Octopus Pro board.

19. "Z1" Motor cable is the motor located in the "Rear Left" as if standing in front of an upright printer and looking towards it. Place the "A" Motor cable into "Motor_3" connector on the Octopus Pro board.

20. "Z2" Motor cable is the motor located in the "Rear Right" as if standing in front of an upright printer and looking towards it. Place the "A" Motor cable into "Motor_4" connector on the Octopus Pro board.

21. "Z3" Motor cable is the motor located in the "Front Right" as if standing in front of an upright printer and looking towards it. Place the "A" Motor cable into "Motor_5" connector on the Octopus Pro board.

22. Bottom Electronic Compartment Fans.  There are two of these fans please splice them together so that one JST connector will feed both fans. Basically you are creating a Y-cable adapter. The "Bottom Electronic Compartment Fans" are connected into "FAN2" connector on the Octopus Pro board.

23. "Filter/Exhaust Fan for the Nevermore Filter" get connected into "FAN3" connector on the Octopus Pro board.

Now the rest of the hook-up is to take care of additional items I have added to this build via Mods: like the "FANS mod"; additional Neopixel LED lights for my side edge panel lighting; additional Neopixel LED lights for the Bottom Electronics case; additional Neopixel LED lights for the Litter Box mod; additional Neopixel LED lights for the Left and right side of TOP panel; additional Neopixel LED lights for the front and back side of the TOP panel; multiple SPST switches to control the Neopixels Lights; additional thermistor wires that are attached the cable chain; ADXL35 connections to the Raspberry Pi; filament runout sensor; PT1000 thermistor wires or a PT100 4-wire sensor cable; endocope wires; a spare Hotend Thermistor wires; ethernet keystone connection; Fans for the Litter Box Mod; USB 2.0 & USB 3.0 Keystone connection; and the BTT's TFTpi50 screen hookup to the Raspberry Pi. I believe that takes care of all the extra items.

I am tired, and it looks like I will have to update my [wiring harness diagram](https://github.com/GadgetAngel/Voron2.4_My_Build_Log/blob/main/Wiring_Harness_Diagram/Voron_2.4_Tool_Head_PCB__Wiring_Harness.pdf) to reflect the changes to the Klicky probe connection and the Filament Sensor (for ERCF connection) to the Octopus Pro board. Furthermore, I apperently need to swap those two locations. I also need to change the LED hook up on the wiring harness diagram.  I have switched from 24VDC LED lights to only using Neopixel lights (which are 5VDC, GND and a data line).

1/13/2022: After looking into the Octopus V1.0/V1.1 and the Octopus Pro V1.0 board's schematic diagrams, I decided to look further into the RGB header of both boards.

From reading the [SN74LVC1G125 chip data sheet on page 5](https://github.com/GadgetAngel/Voron2.4_My_Build_Log/blob/main/Resources/sn74lvc1g125.pdf), I decided some bench testing is needed to see what is going on with the SN74LVC1G125 voltage lines and how it is effecting the Octopus' ability to send data appropriatly to the first NeoPixel.

Here is a picture of how I see the problem at this time:

JPG of Understanding_the_Octopus_RBD_header_issue

[Here is the online Voltage drop calculator I used.](https://www.rapidtables.com/calc/wire/voltage-drop-calculator.html)

Here is a table showing American Wire Gauge current rating: https://www.engineeringtoolbox.com/wire-gauges-d_419.html

Edited 1/25/2022:
After testing and working with other Voron users, it has been decided that the SN74LVC1G125 chip that is being used on the Octopus board (V1.1 and the Pro versions) is **not** doing a sufficient job for the stealthburner NeoPixels.  

The length of the wire and reflections on the data signal line are causing distorations in the RGB data signal.  Therefore, to ensure that the data line will work for any size Voron 2.4 build, I recommend installing a [logic level converter](https://www.amazon.com/gp/product/B01N30ZCW9).  I have updated the "AC Wiring Diagram" to demonstrate the wiring involved.

## A Picture of the "Voron 2.4 AC Electrical Wiring Diagram" for QUEEN:

You can download the JPG file for the "Voron 2.4 AC Wiring Diagram" by clicking on the filename ["Voron_2.4_Electronics_Case_Wiring_Diagram_AC_wiring.jpg"](../images/Voron_2.4_Electronics_Case_Wiring_Diagram_AC_wiring.jpg) and then hit the download button.

JPG of Voron2.4_AC_Electrical_Wiring_Diagram

## The PDF file of the "Voron 2.4 AC Electrical Wiring Diagram" for QUEEN:

The PDF file looks the same as the JPG file. You can enlarge the image for both file types to get all the details.

To download the PDF just click on the filename ["Voron_2.4_Electronics_Case_Wiring_Diagram_AC_wiring.pdf"](../images/Voron_2.4_Electronics_Case_Wiring_Diagram_AC_wiring.pdf) and hit the download button.

## A Picture of the "Voron 2.4 DC Electrical Wiring Diagram" for QUEEN:

Coming Soon.

<!--- You can download the JPG file for the "Wiring Harness" by clicking on the filename ["Voron_2.4_Tool_Head_PCB__Wiring_Harness.jpg"](https://github.com/GadgetAngel/Voron2.4_My_Build_Log/blob/main/Voron2.4_My_Build_Log/Wiring_Harness_Diagram/Voron_2.4_Tool_Head_PCB__Wiring_Harness.jpg) or the filename ["Voron_2.4_Tool_Head_PCB__Wiring_Harness_400ppi.jpg"](https://github.com/GadgetAngel/Voron2.4_My_Build_Log/blob/main/Voron2.4_My_Build_Log/Wiring_Harness_Diagram/Voron_2.4_Tool_Head_PCB__Wiring_Harness_400ppi.jpg) and then hit the download button.

Again, to download the PDF just click on the filename ["Voron_2.4_Tool_Head_PCB__Wiring_Harness.pdf"](https://github.com/GadgetAngel/Voron2.4_My_Build_Log/blob/main/Voron2.4_My_Build_Log/Wiring_Harness_Diagram/Voron_2.4_Tool_Head_PCB__Wiring_Harness.pdf) or the filename ["Voron_2.4_Tool_Head_PCB__Wiring_Harness_400ppi.pdf"](https://github.com/GadgetAngel/Voron2.4_My_Build_Log/blob/main/Voron2.4_My_Build_Log/Wiring_Harness_Diagram/Voron_2.4_Tool_Head_PCB__Wiring_Harness_400ppi.pdf) and hit the download button.

 ![JPG of Wiring_Harness](Voron_2.4_Tool_Head_PCB__Wiring_Harness.jpg) -->

## The PDF file of the "Voron 2.4 DC Electrical Wiring Diagram" for QUEEN:

Coming Soon.

<!--- The PDF file looks the same as the JPG file. You can enlarge the image for both file types to get all the details.

You can view the PDF in your browser by clicking on the filename ["Voron_2.4_Tool_Head_PCB__Wiring_Harness.pdf"](https://github.com/GadgetAngel/Voron2.4_My_Build_Log/blob/main/Voron2.4_My_Build_Log/Wiring_Harness_Diagram/Voron_2.4_Tool_Head_PCB__Wiring_Harness.pdf) and then hit the download button.

You can view an even higher resolution image when you view the PDF in your browser by clicking on the filename ["Voron_2.4_Tool_Head_PCB__Wiring_Harness_400ppi.pdf"](https://github.com/GadgetAngel/Voron2.4_My_Build_Log/blob/main/Voron2.4_My_Build_Log/Wiring_Harness_Diagram/Voron_2.4_Tool_Head_PCB__Wiring_Harness_400ppi.pdf) and then hit the download button. -->

---

## What is the Litter Box Mod?

Please go to [My Litter Box Mod folder](https://github.com/GadgetAngel/Voron2.4_My_Build_Log/tree/main/Electronics_Case_Wiring_Diagram/Litter_Box_Mod).

## Want more information about the "Litter Box" Mod?

Please go to [My Litter Box Mod folder](https://github.com/GadgetAngel/Voron2.4_My_Build_Log/tree/main/Electronics_Case_Wiring_Diagram/Litter_Box_Mod).

## A Picture of the "Voron 2.4 AC Electrical Wire Routing Diagram" for QUEEN:

Coming Soon.

I intend to use snapshots from the 3D model I developed for the QUEEN printer, showing you the acutal route I will use for each wire.

<!--- You can download the JPG file for this "Wiring Harness" by clicking on the filename ["Voron_2.4_Tool_Head_PCB__Wiring_Harness.jpg"](https://github.com/GadgetAngel/Voron2.4_My_Build_Log/blob/main/Voron2.4_My_Build_Log/Wiring_Harness_Diagram/Voron_2.4_Tool_Head_PCB__Wiring_Harness.jpg) or the filename ["Voron_2.4_Tool_Head_PCB__Wiring_Harness_400ppi.jpg"](https://github.com/GadgetAngel/Voron2.4_My_Build_Log/blob/main/Voron2.4_My_Build_Log/Wiring_Harness_Diagram/Voron_2.4_Tool_Head_PCB__Wiring_Harness_400ppi.jpg) and then hit the download button.

Again, to download the PDF just click on the filename ["Voron_2.4_Tool_Head_PCB__Wiring_Harness.pdf"](https://github.com/GadgetAngel/Voron2.4_My_Build_Log/blob/main/Voron2.4_My_Build_Log/Wiring_Harness_Diagram/Voron_2.4_Tool_Head_PCB__Wiring_Harness.pdf) or the filename ["Voron_2.4_Tool_Head_PCB__Wiring_Harness_400ppi.pdf"](https://github.com/GadgetAngel/Voron2.4_My_Build_Log/blob/main/Voron2.4_My_Build_Log/Wiring_Harness_Diagram/Voron_2.4_Tool_Head_PCB__Wiring_Harness_400ppi.pdf) and hit the download button.

 ![JPG of Wiring_Harness](Voron_2.4_Tool_Head_PCB__Wiring_Harness.jpg) -->

## The PDF file of the "Voron 2.4 AC Electrical Wire Routing Diagram" for QUEEN:

Coming Soon.

I intend to use snapshots from the 3D model I developed for the QUEEN printer, showing you the acutal route I will use for each wire.

<!--- The PDF file looks the same as the JPG file. You can enlarge the image for both file types to get all the details.

You can view the PDF in your browser by clicking on the filename ["Voron_2.4_Tool_Head_PCB__Wiring_Harness.pdf"](https://github.com/GadgetAngel/Voron2.4_My_Build_Log/blob/main/Voron2.4_My_Build_Log/Wiring_Harness_Diagram/Voron_2.4_Tool_Head_PCB__Wiring_Harness.pdf) and then hit the download button.

You can view an even higher resolution image when you view the PDF in your browser by clicking on the filename ["Voron_2.4_Tool_Head_PCB__Wiring_Harness_400ppi.pdf"](https://github.com/GadgetAngel/Voron2.4_My_Build_Log/blob/main/Voron2.4_My_Build_Log/Wiring_Harness_Diagram/Voron_2.4_Tool_Head_PCB__Wiring_Harness_400ppi.pdf) and then hit the download button. -->

## A Picture of the "Voron 2.4 DC Electrical Wire Routing Diagram" for QUEEN:

Coming Soon.

I intend to use snapshots from the 3D model I developed for the QUEEN printer, showing you the acutal route I will use for each wire.

<!--- You can download the JPG file for this "Wiring Harness" by clicking on the filename ["Voron_2.4_Tool_Head_PCB__Wiring_Harness.jpg"](https://github.com/GadgetAngel/Voron2.4_My_Build_Log/blob/main/Voron2.4_My_Build_Log/Wiring_Harness_Diagram/Voron_2.4_Tool_Head_PCB__Wiring_Harness.jpg) or the filename ["Voron_2.4_Tool_Head_PCB__Wiring_Harness_400ppi.jpg"](https://github.com/GadgetAngel/Voron2.4_My_Build_Log/blob/main/Voron2.4_My_Build_Log/Wiring_Harness_Diagram/Voron_2.4_Tool_Head_PCB__Wiring_Harness_400ppi.jpg) and then hit the download button.

Again, to download the PDF just click on the filename ["Voron_2.4_Tool_Head_PCB__Wiring_Harness.pdf"](https://github.com/GadgetAngel/Voron2.4_My_Build_Log/blob/main/Voron2.4_My_Build_Log/Wiring_Harness_Diagram/Voron_2.4_Tool_Head_PCB__Wiring_Harness.pdf) or the filename ["Voron_2.4_Tool_Head_PCB__Wiring_Harness_400ppi.pdf"](https://github.com/GadgetAngel/Voron2.4_My_Build_Log/blob/main/Voron2.4_My_Build_Log/Wiring_Harness_Diagram/Voron_2.4_Tool_Head_PCB__Wiring_Harness_400ppi.pdf) and hit the download button.

 ![JPG of Wiring_Harness](Voron_2.4_Tool_Head_PCB__Wiring_Harness.jpg) -->

## The PDF file of the "Voron 2.4 DC Electrical Wire Routing Diagram" for QUEEN:

Coming Soon.

I intend to use snapshots from the 3D model I developed for the QUEEN printer, showing you the acutal route I will use for each wire.

<!--- The PDF file looks the same as the JPG file. You can enlarge the image for both file types to get all the details.

You can view the PDF in your browser by clicking on the filename ["Voron_2.4_Tool_Head_PCB__Wiring_Harness.pdf"](https://github.com/GadgetAngel/Voron2.4_My_Build_Log/blob/main/Voron2.4_My_Build_Log/Wiring_Harness_Diagram/Voron_2.4_Tool_Head_PCB__Wiring_Harness.pdf) and then hit the download button.

You can view an even higher resolution image when you view the PDF in your browser by clicking on the filename ["Voron_2.4_Tool_Head_PCB__Wiring_Harness_400ppi.pdf"](https://github.com/GadgetAngel/Voron2.4_My_Build_Log/blob/main/Voron2.4_My_Build_Log/Wiring_Harness_Diagram/Voron_2.4_Tool_Head_PCB__Wiring_Harness_400ppi.pdf) and then hit the download button. -->

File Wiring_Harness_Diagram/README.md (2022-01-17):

# This repositoy uses LFS extension

```
I use Git for Windows with VScode to manage this repository.  I also use Git LFS extensions for all the files.

Install Git with LFS extensions: https://git-lfs.github.com/

To Download the whole repository do the following: select the "Clone or download button" and
click on "paste to clipboard" button so you can place the URL for the GitHub repository
to the clipboard. Now Open Git Bash.  Change the current working directory to the location
where you want the cloned directory.
Type git clone, and then paste the URL you copied earlier.
$ git clone https://github.com/GadgetAngel/Voron2.4_My_Build_Log.git
Press Enter to create your local clone.
Now open Window explorer to the location of local clone.
```
## This whole repository can be downloaded as one large zip file from my Google Drive at: (if downloading via LFS is giving you are hard time)

## xxxxxxxxxxxxxxxxxxxxxxxxxxxxxxxxxxxxxxxxxxxxxxxxxxxxxxx

# Wiring Harness for QUEEN (my Voron 2.4 build):

This repository contains JPG and PDF files for the wiring harness for QUEEN.

### The PDF file of the "Wiring Harness" for QUEEN:

The PDF file looks the same as the JPG file. You can enlarge the image for both file types to get all the details.

You can view the PDF in your browser by clicking on the filename ["Voron_2.4_Tool_Head_PCB__Wiring_Harness.pdf"](https://github.com/GadgetAngel/Voron2.4_My_Build_Log/blob/main/Wiring_Harness_Diagram/Voron_2.4_Tool_Head_PCB__Wiring_Harness.pdf) and then hit the download button.

Furthermore, you can view an even higher resolution image (give it a minute or two to load, it takes longer due to the higher resolution) when you view the PDF in your browser by clicking on the filename ["Voron_2.4_Tool_Head_PCB__Wiring_Harness_400ppi.pdf"](https://github.com/GadgetAngel/Voron2.4_My_Build_Log/blob/main/Wiring_Harness_Diagram/Voron_2.4_Tool_Head_PCB__Wiring_Harness_400ppi.pdf) and then hit the download button.

## A Picture of the "Wiring Harness" for QUEEN:

This is the wiring harness diagram I developed for my Voron 2.4 build:

You can download the JPG file for this "Wiring_Harness_Diagram" by clicking on the filename ["Voron_2.4_Tool_Head_PCB__Wiring_Harness.jpg"](https://github.com/GadgetAngel/Voron2.4_My_Build_Log/blob/main/Wiring_Harness_Diagram/Voron_2.4_Tool_Head_PCB__Wiring_Harness.jpg).

 You can view an even higher resolution image (give it a minute or two to load, it takes longer due to the higher resolution) when you view the JPG in your browser by clicking on the filename ["Voron_2.4_Tool_Head_PCB__Wiring_Harness_400ppi.jpg"](https://github.com/GadgetAngel/Voron2.4_My_Build_Log/blob/main/Wiring_Harness_Diagram/Voron_2.4_Tool_Head_PCB__Wiring_Harness_400ppi.jpg) and then hit the download button.

Again, to download the PDF just click on the filename ["Voron_2.4_Tool_Head_PCB__Wiring_Harness.pdf"](https://github.com/GadgetAngel/Voron2.4_My_Build_Log/blob/main/Wiring_Harness_Diagram/Voron_2.4_Tool_Head_PCB__Wiring_Harness.pdf) or the filename ["Voron_2.4_Tool_Head_PCB__Wiring_Harness_400ppi.pdf"](https://github.com/GadgetAngel/Voron2.4_My_Build_Log/blob/main/Wiring_Harness_Diagram/Voron_2.4_Tool_Head_PCB__Wiring_Harness_400ppi.pdf) and hit the download button.

Please take notice of the Notes on the "Wiring_Harness_Diagram".  To ensure you see it, I am going to repeat it here:

Note about the Hartk1213 v3.rabbit board:
If the jumper pads on the back of the v3.rabbit are configured
incorrectly you could end up damaging your Octopus Pro mother board!!

Because there are two different versions of this Toolhead board around (let’s call them version #1, and version #2), before powering on your printer, please ensure that the jumper pads on the back of the v3.rabbit Toolhead board are properly configure for your FANS and ABL!

How to tell which version of the v3.rabbit Toolhead board you own:

If you turn the board over on its back, you will see a bank of jumper pads.  For version #1 of the v3.rabbit Toolhead board has 4 columns by 3 rows of jumper pads.  For version #2 of v3.rabbit Toolhead board has 3 columns by 3 rows of jumper pads.  If you have version #1 of the v3.rabbit Toolhead board (4 columns by 3 rows of jumper pads) than you are responsible for bridging the jumper pads to your desired voltage (in my case I would solder a bridge to 24VDC for ABL, PCF, HEF, and FS).  If you have version #2 of the v3.rabbit Toolhead board (3 columns by 3 rows of jumper pads) than all the selectable voltages default to 24VDC!

Here is what the labels mean:
ABL means auto bed leveling or an inductive probe or the proximity sensor connector; PCF means Part Cooling Fan; HEF means Hotend Fan; and FS means Filament Switch Sensor.

For version #1 of the v3.rabbit board, the columns are labeled from left to right: ABL, PCF, HEF, FS. For version #2 of the v3.rabbit board, the columns are labeled from left to right: ABL, PCF, HEF.

Version #1 and version #2 the rows are: 1st row is 24VDC; 2nd row is (ABL, PCF, or HEF, {only on Version #1 FS}); and 3rd row is 5VDC.

If you have version #2, and you want 5VDC, you are going to cut the trace to the 24VDC on the desired PIN (ABL, PCF or HEF)!

JPG of wiring harness Diagram

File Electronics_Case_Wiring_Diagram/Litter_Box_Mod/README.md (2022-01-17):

# This repositoy uses LFS extension

```
I use Git for Windows with VScode to manage this repository.  I also use Git LFS extensions for all the files.

Install Git with LFS extensions: https://git-lfs.github.com/

To Download the whole repository do the following: select the "Clone or download button" and
click on "paste to clipboard" button so you can place the URL for the GitHub repository
to the clipboard. Now Open Git Bash.  Change the current working directory to the location
where you want the cloned directory.
Type git clone, and then paste the URL you copied earlier.
$ git clone https://github.com/GadgetAngel/Voron2.4_My_Build_Log.git
Press Enter to create your local clone.
Now open Window explorer to the location of local clone.
```
## This whole repository can be downloaded as one large zip file from my Google Drive at: (if downloading via LFS is giving you are hard time)

## xxxxxxxxxxxxxxxxxxxxxxxxxxxxxxxxxxxxxxxx

### What is the Litter Box Mod?

Think of the "Litter Box" as the poor man's DOOM mod.  Basically, I split the electronics up into two sections. AC electronics go in the "bottom case" on the Voron 2.4 250 mm³ and the standard electronics boards go in the "Litter Box" mod.  Instead of putting the "standard electronics" on the TOP of the printer (as the DOOM MOD does), I put the boards on the BACK of the Voron 2.4 250 mm³ build.  I did this, so I would **not** have to buy another wiring harness. I can use the wiring harnesses that are pre-made.  For the DOOM Mod the pre-made wiring harness will not work because it will not be long enough, but the "Litter Box" mod allows you to use the pre-made wiring harness.  I also designed the "Litter Box" mod so that one can not see the "Litter Box" mod is attached to the printer unless you are viewing the Voron from the side.

I also designed the "Litter Box" Mod so that I did not have to cut out a lot of different holes in the Coraplast top/bottom panels or the two Coraplast side panels.  Furthermore, I also designed an "Extended" skirt, so that the back skirt is not hidden underneath the mod, instead the back skirt has been moved out.  This then required me to design an extended Bottom panel to cover the AC socket plugs.  To hold the extended Bottom panel in place, I had to design two clips interfaces blocks so that I could reuse the bottom magnetic clips from [Hernsl's "Bottom_panel_mag_clip Mod"](https://github.com/VoronDesign/VoronUsers/tree/master/printer_mods/hernsl/bottom_panel_mag_clip).

Here is a video Tour:

Litter Box Video Tour with Narration Done By GadgetAngel (https://youtu.be/gklbsIQtgYg)

### So how did I start this "Litter Box" Mod?

Since I knew I needed more space I started to search by looking at the CAD models of all the different Voron 3D printer models.  I also knew that I would need to learn Fusion 360, if I wanted to design this mod.

I watched some YouTube videos from [Lars Christensen](https://www.youtube.com/watch?v=DVtzuj7_F9g), and bravely went down this road.  After a couple of days my hands started to hurt, so I look into buying a [space mouse](https://3dconnexion.com/uk/product/spacemouse-wireless/).  A space mouse allows you to turn the Fusion 360 model like you are holding the part in your own hands.

Before I bought the space mouse, I converted by free license for Fusion 360 into a subscription license.  After doing this I uploaded all the Voron printer models and start to look around.

On the Voron 1.8 there is a backpack electronic case that holds the DC electronics.  I decide to start with this item and develop my "Litter Box" Mod from it.

On the Voron 1.8 the backpack electronic case is inside the frame of the printer.  My litter box will be on the outside of the frame.  On the Voron 1.8 backpack electronics do not have compressor feet because the feet are actually on the end of the extrusion (a 3D printed part).

So I decide to replace the Voron 1.8 backpack electronic case feet with mirror images of the upper support brakets.

To attach the DIN rails to the back of the machine I found the [hijax_pl's din_rail_mount - the angled DIN mount version](https://github.com/VoronDesign/VoronUsers/tree/master/printer_mods/hijax_pl/din_rail_mount).  After doing the first through 4th revisions of the Litter Box Mod, I finally decided to check out the DIN mounts from the Trident model.  After I saw how the Trident version of DIN mounting looked, I started to use and design items that would utilize the Trident DIN mounting system.

So, my brackets that hold the DIN rail to the back of the Voron printer first used [hijax_pl's angled DIN mount](https://github.com/VoronDesign/VoronUsers/blob/master/printer_mods/hijax_pl/din_rail_mount/din_rail_mount_angle_panel.step). But when I looked at the outline for how the DIN rail fit into his part, I noticed that if your printer is not dialed in properly, this part may cause issues due to the low clearence in the hole for the outline of the DIN rail.  While looking at the Trident 3D printed parts, the DIN mount from Trident has a larger clearnece for the DIN rail but utilizes an M3 screw to hold the DIN rail down with frictions. So I changed out my design to use the Trident version of the DIN rail by merging the two mounts together into.  The Angled part of the mount from hijax_pl got added to the Trident DIN mount.

Since I did not want to drill a lot of holes in my Coraplast panels for the top/near_bottom and the two side panels of the Litter Box, I decided not to make a curvy version of the DIN mount.  I keeped it in a block shape. That way when all the support brackets are installed the brackets have the same height.  The panel for the sides are the same.  The Top is the same as the near_bottom except the near_bottom panel has an oval slot shape cut out so that you can pass wires from the bottom elctronics case up to the Litter box on the back of the printer. At this time, I do not plan on installing the near_bottom panel because I need to mount WAGO nuts on the extrusions and the near_bottom panel will hit the WAGo nuts.  Since I added an extended Bottom panel the near_bottom panel is really not needed.

I first tackled the Corner Support brackets.  I knew I wanted to design for different Back Panel thicknesses.  My mod has three versions (3 mm, 4 mm and 6 mm).

The Corner Support Brackets from the Voron 1.8 attach to a vertical extursion from the inside side of the frame.  The litter box has to hang off the back, so I do not have access to the inside of the extrusion unless I cut holes in the Voron 2.4 Back panel.

I decide that I did not want to cut holes in the Voron 2.4 Back Panel.  So I added to the DIN mounting bracket.  The 4 Corner Support Brackets are integrated into the DIN Mounting Brackets.  I designed to use three (3) M2x20 Socket Head Screws (which have counterbore holes for the M2 screw head) and I designed to use M2 heat set inserts to secure the DIN mount bracket to the Corner Support Bracket.

The M2 heat set inserts will be placed inside the 4 Coroner Support Brackets. The M2 heat set insets you will need to buy can be purchased from [AliExpress](https://www.aliexpress.com/item/4000232858343.html?spm=a2g0s.9042311.0.0.dcd44c4dya58ZN) - the recommended vendor from the Voron 2.4 sourcing guide. Buy the "M2 X D4.0 X L5.0" version of the M2 heat set inserts. I suppose you can use any M2 heat set insert as long as it is not wider than 4 mm and longer the 5 mm.

The M2x20 Socket Head Screws can be purchased anywhere. I bought from [McMaster-Carr](https://www.mcmaster.com/catalog/127/3366), but you can easily use ones from [Amazon](https://www.amazon.com/gp/product/B07H4MG7TC).

I could not use M3 screw because the holes were too big for the design I started off with.  Furthermore, I first created a DIN bracket that had a slot built into the bracket to allow the Coraplast panel to slide into the slot. But after examining the bracket design, I opted to remove the slot to make the DIN bracket stronger.  It is more important that the DIN mounts are solid and can hold the electronics board, PSU and DIN rail to the back panel.

But since I started out with a slotted DIN mount, I designed using M2 screws because the M3 screws would not fit.  I suppose if someone wanted to mod my mod you could create an M3 version but M2x20 screws are not hard to come by.

The next issue in my design arose when I noticed that the Side Panel would stick out on either side of the extrusion. So when you looked from the front of the printer you would ask yourself, "what is that black plastic in the middle of the back of the printer?".  I decided to offset the Corner Support brackets so that the Litter Box could not be seen from the front of the Voron 2.4.

The next issue to arise was the back skirt.  It was sitting below the litter box but under the litter box.  I wanted the back skirt to be flush with the back panel of the litter box.  So the problem was how to extend the skirt?  I remebered that I read some talk about the Voron 2.4 300 mm³ printer's sit heavily on the back two feet of the printer.  So my next concern was would the printer tilt over with the Litter Box on the back?  To solve the extended skirt and the possibility of tilting I decided to create two dummy Z drive/feet combos (basically creating two new feet).  These dummy Z drive feet look like the real Z drives, but they are just made out of 3D printed plastic.  This way you can match the feet up if you want.  Since I am using the [Edwardyeeks' "V2.4_z_drive_motor_tensioner_mod"](https://github.com/VoronDesign/VoronUsers/tree/master/printer_mods/edwardyeeks/V2.4_z_drive_motor_tensioner_mod) and [Spaghetti-Bolognese's "Z Driver System Mods"](https://github.com/VoronDesign/VoronUsers/tree/master/printer_mods/Spaghetti-Bolognese/Z_drive_motor_mount) combo on my printer, I choose to just stick with the Voron 2.4 original Z drive feet.  This way if you choose not to do the Z driver mods the feet will all match. By adding two feet and using the Z Drive block the "side extended skirt" is created.

So now I needed to design a way to mount the back skirt (the same one you would normally use) to the bottom of the Litter Box.  Since the Litter Box uses only 2020 extrusions that was really not a problem.

The Litter Box uses the following 2020 extrusions lengths:

Take the Frame Width for your build size (for me 250 mm³ my frame width is 410 mm) and subtract 56 mm to obtain the Top and Bottom extrusion length needed for the Litter Box. To find the length of the Side 2020 extrusions take your frame width and subtract 182 mm.

So for my 250 mm³ build I will need the following 2020 extrusions:

1. Top/Bottom 2020 Extrusion (frame width - 56 mm) Length = 354 mm

2. Two Side 2020 Extrusions (rame width - 182 mm) Lenght = 228 mm

The Coraplast panels are 4 mm thick (or what ever material you want to use, I plan on carbon fiber panels after I test out the Coraplast panels) dimensions can be calculated as follows:

The height of the Top/Bottom Panels, the height of the Right/Left Side Panels, the height of the Front Panel and the width of the Right/Left Side Panels will stay the same for all build sizes. The only dimension that will change is the distance between your two back vertical extrusions which will only affect the Top/Bottom width and the Front Panel width:

Top/Bottom Coraplast panels' dimensions for the Litter Box Mod:

Height = 93 mm
Width = (frame width - 53.5)

Left/Right Side Coraplast Panels' dimensions for the Litter Box Mod:

Height = 242 mm
Width = 75.5 mm

Front Coraplast Panel's dimensions for Litter Box Mod:

Height = 242 mm
Width = (frame width - 55.5)

There are cut-outs that need to be made for the front panel, I need to do the drawing for this panel. I will publish it here when I get it done. I will do it in .dxf format and .pdf format. Furthermore, I will even create a .svg file for it.

So for **my 250 mm³ QUEEN Build** I will use the following dimensions for my Coraplast panels:

Top/Bottom Coraplast Panels dimensions for the Litter Box Mod on a 250 mm³ Voron 2.4 Build:

Height = 93 mm
Width = (frame width {410} - 53.5) = 356.5 mm

Left/Right Side Coraplast Panels' dimensions for the Litter Box Mod on a 250 mm³ Voron 2.4 Build:

Height = 242 mm
Width = 75.5 mm

Front Coraplast Panel's dimensions for Litter Box Mod on a 250 mm³ Voron 2.4 Build:

Height = 242 mm
Width = (frame width {410} - 55.5) = 354.5

(BTW, you will notice that the width of the Front panel is only 2 mm shorter than the Front Panel width = (Top/Bottom Width - 2 mm))!

Back to what I was talking about, how did I mount the back skirt to the litter box mod?  I wanted the height of the back skirt to be exactly as it is on the original Voron 2.4 printer.  So I decided to create an "Interface Bar".  The Height of this interface bar will change depending on how high you mount the Litter Box to the two back vertical extrusions.  I choose to place the Litter Box as low as I could go on the back two vertical 2020 extrusions.

So my mod fixes the Litter Box to be mounted at the bottom of the two back 2020 extrusions and my 3D model has it placed at that location.

Since I decided on my mount location, I design the inteface bar (which is a 3D-printed part). In the 3D model you see the word's VORON 2.4 V2.1234, I use the Interface Bar as a way to register your Voron serial number when you get one.  So this part has lettering which will be printed with "VORON 2.4" and "V2.1234". You can reprint this part and remount it after you get your serial number.

The Interface Bar is just a block of plastic with a slotted hole, that allows the screw to pass through to the Litter Box Bottom 2020 extrusion.  You will need to use longer M3 screw to mount your back skirt pieces, but you will not have to reprint your back skirt peices.  You just need to print the Interface Bar A/B and the Foot Interface A/B pieces.

What is the Foot Interface A/B piece.  The Foot Interface is how the two dummy feet get mounted to the Bottom 2020 extrusion of the Voron 2.4 printer.  The Foot Interface A/B comes in three sizes to accomdate three different Voron 2.4 Back Panel thickness sizes (3 mm, 4 mm, and 6 mm).

Since the Litter Box does not cover the totallity of the Back Panel, I wanted the ability to move the electronics boards up or down from the DIN rail to help with wire routing.  I ended up designing a sliding mounting system for the electronics.  Basically a nut and bolt are used to the two sliding haves together, and I have designed these mounts to accomodate as many of the Voron DIN clips as I could (Trident DIN clips and Voron 2.4 DIN clips)

These new sliding mounts are listed under the Litter Box electronics mod.  I also designed some stablizing arms for the UHP PSU models.  The Stablizing arm is not bolted down to the PSU but stops the PSU from shifing horizontally.

<!--- You can download the JPG file for this "Wiring Harness" by clicking on the filename ["Voron_2.4_Tool_Head_PCB__Wiring_Harness.jpg"](https://github.com/GadgetAngel/Voron2.4_My_Build_Log/blob/main/Voron2.4_My_Build_Log/Wiring_Harness_Diagram/Voron_2.4_Tool_Head_PCB__Wiring_Harness.jpg) or the filename ["Voron_2.4_Tool_Head_PCB__Wiring_Harness_400ppi.jpg"](https://github.com/GadgetAngel/Voron2.4_My_Build_Log/blob/main/Voron2.4_My_Build_Log/Wiring_Harness_Diagram/Voron_2.4_Tool_Head_PCB__Wiring_Harness_400ppi.jpg) and then hit the download button.

Again, to download the PDF just click on the filename ["Voron_2.4_Tool_Head_PCB__Wiring_Harness.pdf"](https://github.com/GadgetAngel/Voron2.4_My_Build_Log/blob/main/Voron2.4_My_Build_Log/Wiring_Harness_Diagram/Voron_2.4_Tool_Head_PCB__Wiring_Harness.pdf) or the filename ["Voron_2.4_Tool_Head_PCB__Wiring_Harness_400ppi.pdf"](https://github.com/GadgetAngel/Voron2.4_My_Build_Log/blob/main/Voron2.4_My_Build_Log/Wiring_Harness_Diagram/Voron_2.4_Tool_Head_PCB__Wiring_Harness_400ppi.pdf) and hit the download button.

 ![JPG of Wiring_Harness](Voron_2.4_Tool_Head_PCB__Wiring_Harness.jpg) -->

## A Picture of the "Litter Box" mod for QUEEN:

The "Litter Box" mod is a place to store all you good s..t......LOL

The name is a wink to RCF (a.k.a. RussianCatFood).

I also have posted two videos which give you a roatating view of the QUEEN 3D model.  This is the 3D model I used
to devleop the Litter Box.

1. First look Video: https://youtu.be/x5X1lYImGgg;

2. Second Look Video: https://youtu.be/KOevvhMHMqQ

Here are some still pictures:

The Front View:

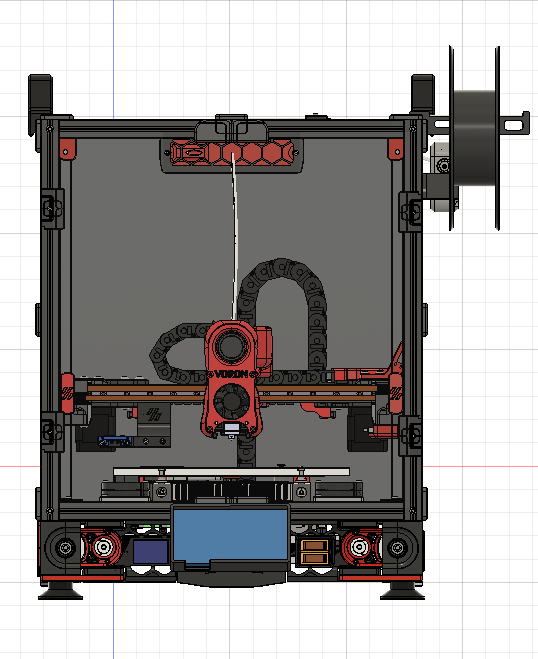
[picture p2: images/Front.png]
"Front View of QUEEN"


 The Litter Box can not be seen, the Voron 2.4 looks actually like a regular Voron 2.4 machine.

The Left Profile View:

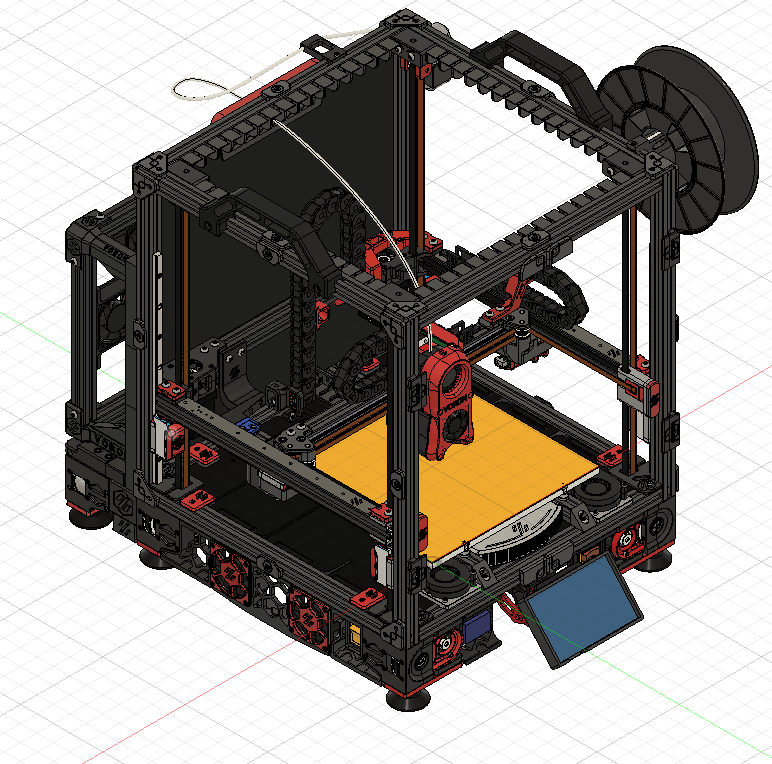
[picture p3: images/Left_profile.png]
"Left Profile View"


This is where you see the Litter Box mod.  The Litter Box mod will hang off the back and over the Back Panel of the Voron 2.4 printer. There is no need to buy another Back Panel since the Litter Box Mod is designed to hold the Back Panel in place instead of the Panel Clips.

The Wide Right View:

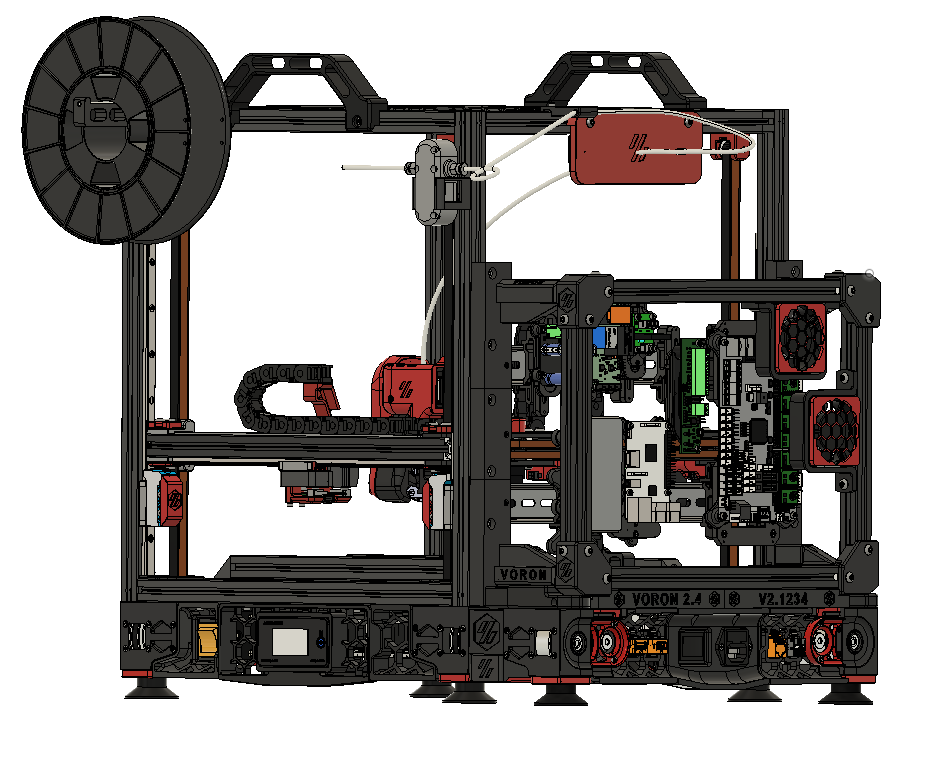
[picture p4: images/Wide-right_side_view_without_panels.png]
"Wide Right View of QUEEN"


The Bottom View with panels:

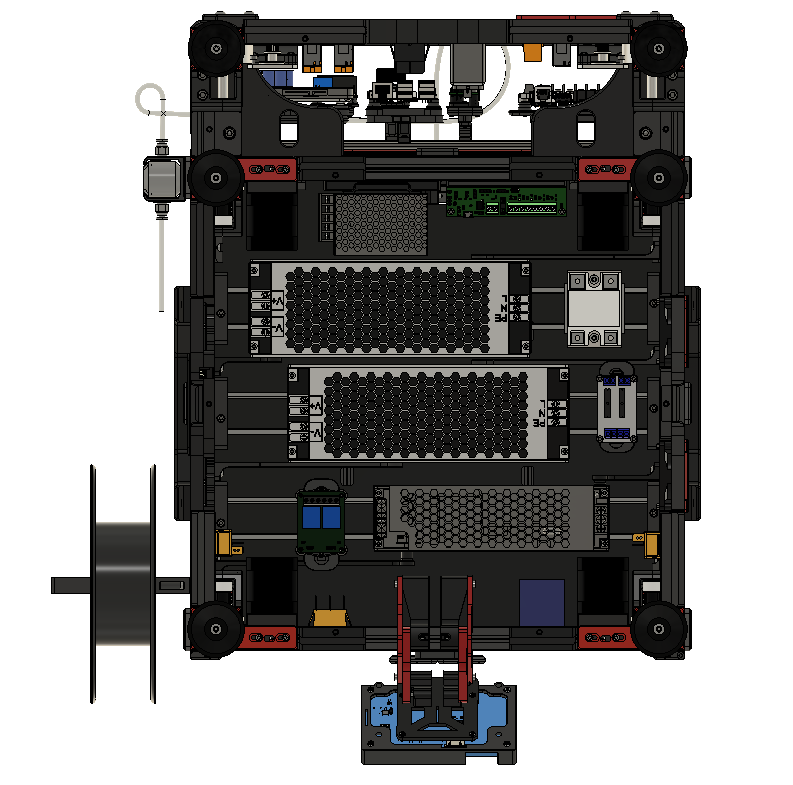
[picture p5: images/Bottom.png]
"Bottom View of QUEEN"


The Bottom View without panels:

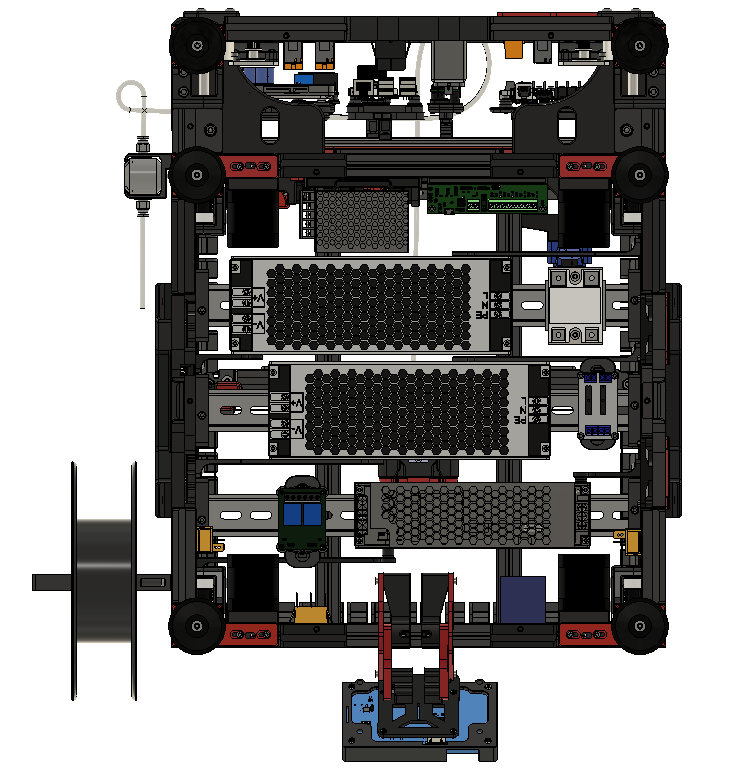
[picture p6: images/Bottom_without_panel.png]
"Naked Bottom View of QUEEN"


The View from the TOP:

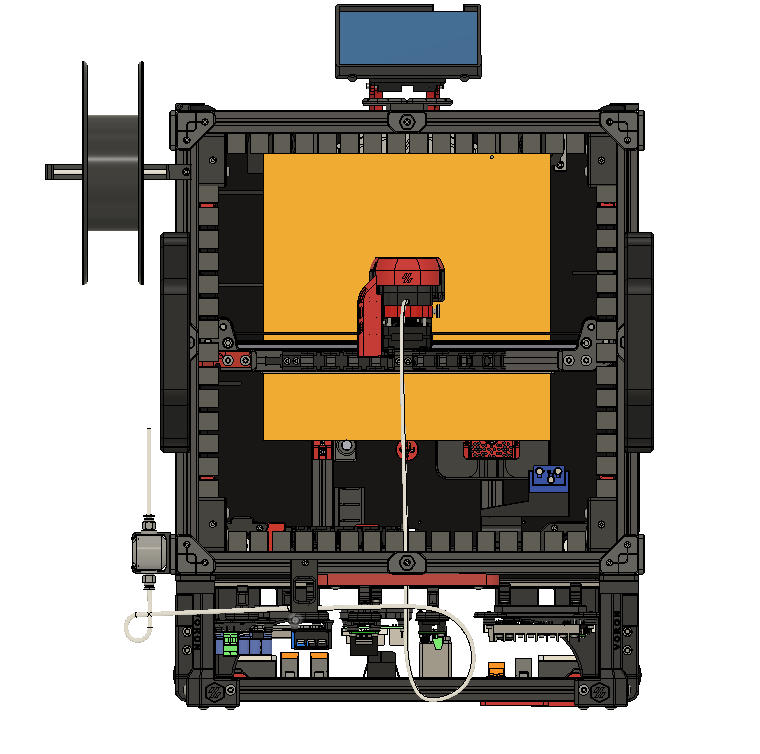
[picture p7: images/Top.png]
"Top View of QUEEN


## Testing exploded video view

UHP-500_PSU_DIN_Mounts_v4

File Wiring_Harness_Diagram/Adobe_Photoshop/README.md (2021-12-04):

# This repositoy uses LFS extension

```
I use Git for Windows with VScode to manage this repository.  I also use Git LFS extensions for all the files.

Install Git with LFS extensions: https://git-lfs.github.com/

To Download the whole repository do the following: select the "Clone or download button" and
click on "paste to clipboard" button so you can place the URL for the GitHub repository
to the clipboard. Now Open Git Bash.  Change the current working directory to the location
where you want the cloned directory.
Type git clone, and then paste the URL you copied earlier.
$ git clone https://github.com/GadgetAngel/Voron2.4_My_Build_Log.git
Press Enter to create your local clone.
Now open Window explorer to the location of local clone.
```

## This whole repository can be downloaded as one large zip file from my Google drive at:  (if downloading via LFS is giving you are hard time)

## xxxxxxxxxxxxxxxxxxxxxxxxxxxxxxxxxxxxxxxxxxxxxxxxxxxxxxx

# Wiring Harness for QUEEN (my Voron 2.4 build):

This repository contains Adobe Photoshop files for the wiring harness for QUEEN.

### The .psb files of the "Wiring Harness" for QUEEN:

There are two .psb files located here.  One is done in 900ppi and the other was produced from the 900ppi version, it is at 300ppi.

Since I do a lot of work in vector graphics, I have found that working in Photoshop at 900ppi makes it easier to convert stuff later to .svg files (if I use a higher ppi than 300).  Most photos are done at 300ppi.

Therefore, just out of habit, I work at 900ppi.  I up convert images to 900ppi using Photoshop.  When I want to produce an image I then down convert to 300ppi from 900ppi.

Since 900ppi produces very large files, I convert my original file down to 300ppi.  I tried uploading the 900ppi file to GitHub but GitHub, even with LFS installed, has an upper file limit of 2GB.

After converting my 5GB 900ppi file to 300ppi the file size was still 4GB. So I compressed each file using WinZip and got the file sizes below 2GB limit.

Use which ever file you want they are both the same.

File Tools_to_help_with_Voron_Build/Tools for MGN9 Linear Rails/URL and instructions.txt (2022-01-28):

https://www.thingiverse.com/thing:3716735

Slot the side pieces in against the balls to hold them in place, then press in the center shim to hold everything together. Slide the carriage onto the end of the rail displacing the tool. Tada, no lost balls and cleaning/greasing is less intimidating.

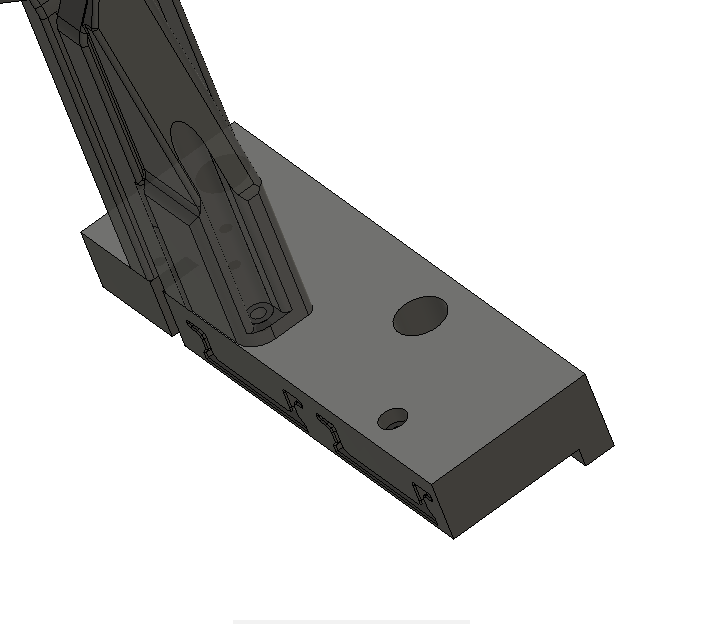
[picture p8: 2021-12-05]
Electronics_Case_Wiring_Diagram/Litter_Box_Mod/Litter_Box_Mod_only_pictures/Bar_Bones_only_pictures/Lower_Left_Corner_bracket_with_Lower_Left_DIN_mount_so_you_can_see_the_DIN_holes_for_the_M3_retaini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

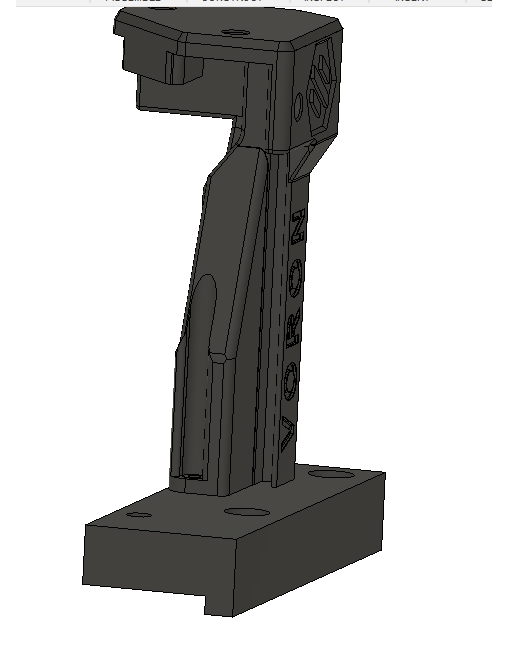
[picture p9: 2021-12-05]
Electronics_Case_Wiring_Diagram/Litter_Box_Mod/Litter_Box_Mod_only_pictures/Bar_Bones_only_pictures/View_so_you_can_see_the_slot_for_the_Side_Panel.png

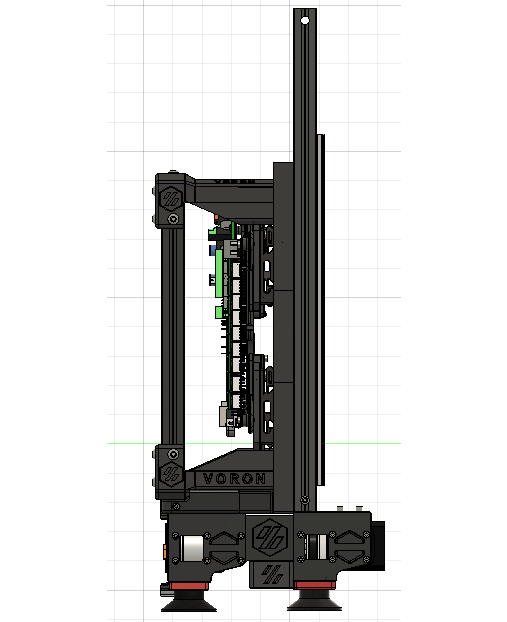
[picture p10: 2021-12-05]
Electronics_Case_Wiring_Diagram/Litter_Box_Mod/Litter_Box_Mod_only_pictures/Left_side_view_Without_Panels.png

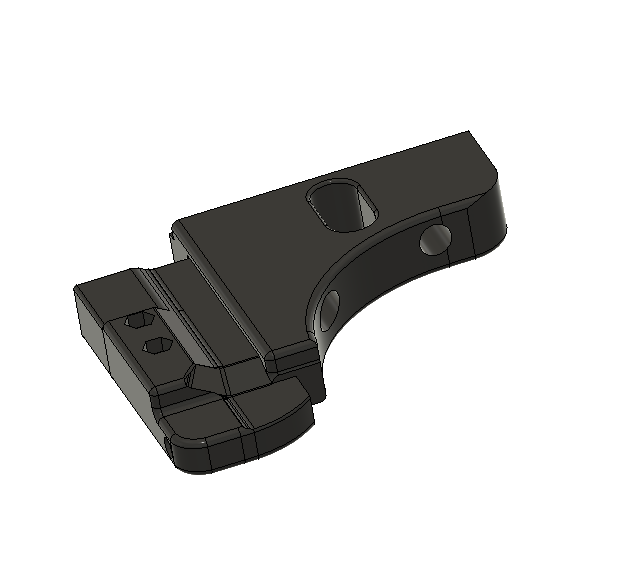
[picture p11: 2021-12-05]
Electronics_Case_Wiring_Diagram/Litter_Box_Mod/Litter_Box_Mod_only_pictures/Bar_Bones_only_pictures/Foot_Interface_A_Back-top_view.png

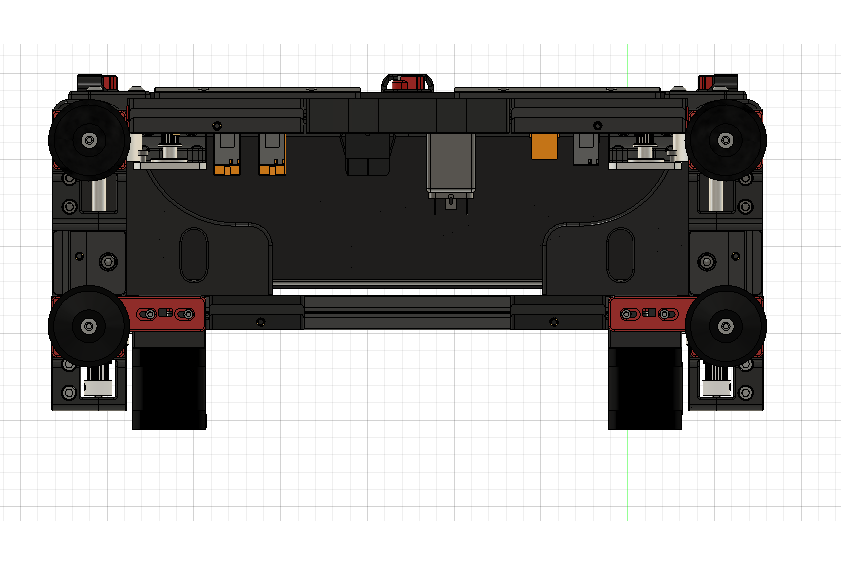
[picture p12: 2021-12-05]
Electronics_Case_Wiring_Diagram/Litter_Box_Mod/Litter_Box_Mod_only_pictures/Bottom_without_the_bottom_extended_panel.png

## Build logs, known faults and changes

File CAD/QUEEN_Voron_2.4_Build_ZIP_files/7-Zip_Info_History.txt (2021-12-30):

HISTORY of the 7-Zip
--------------------

21.07          2021-12-26
-------------------------
- 7-Zip now can extract VHDX disk images (Microsoft Hyper-V Virtual Hard Disk v2 format).
- New switches: -spm and -im!{file_path} to exclude directories from processing 
    for specified paths that don't contain path separator character at the end of path.
- In the "Add to Archive" window, now it is allowed to use -m prefix for "Parameters" 
  field as in command line: -mparam.
- The sorting order of files in archives was slightly changed to be more consistent
  for cases where the name of some directory is the same as the prefix part of the name
  of another directory or file.
- TAR archives created by 7-Zip now are more consistent with archives created by GNU TAR program.

21.06          2021-11-24
-------------------------
- The window "Add to Archive" now allows to set a limit on memory usage (RAM) 
  that will be used for compressing.
- New switch -mmemuse={N}g / -mmemuse=p{N} to set a limit on memory usage (RAM) 
  for compressing and decompressing.
- Bug in versions 21.00-21.05 was fixed:
  7-Zip didn't set attributes of directories during archive extracting.
- Some bugs were fixed.

21.04 beta     2021-11-02
-------------------------
- 7-Zip now reduces the number of working CPU threads for compression,
  if RAM size is not enough for compression with big LZMA2 dictionary.
- 7-Zip now can create and check "file.sha256" text files that contain the list 
  of file names and SHA-256 checksums in format compatible with sha256sum program.
  7-Zip can work with such checksum files as with archives,
  but these files don't contain	real file data.
  The context menu commands to create and test "sha256" files:
    7-Zip  /  CRC SHA  /  SHA-256 -> file.sha256
    7-Zip  /  CRC SHA  /  Test Archive : Checksum
  The commands for command line version:
    7z a -thash file.sha256 *.txt
    7z t -thash file.sha256
    7z t -thash -shd. file.sha256 
  New -shd{dir_path} switch to set the directory that is used to check files 
  referenced by "file.sha256" file for "Test" operation. 
  If -shd{dir_path} is not specified, 7-Zip uses the directory where "file.sha256" is stored.  
- New -xtd switch to exclude directory metadata records from processing.

21.03 beta     2021-07-20
-------------------------
- The maximum dictionary size for LZMA/LZMA2 compressing was increased to 4 GB (3840 MiB).
- Minor speed optimizations in LZMA/LZMA2 compressing.

21.02 alpha    2021-05-06
-------------------------
- 7-Zip now writes additional field for filename in UTF-8 encoding to zip archives.
  It allows to extract correct file name from zip archives on different systems.
- The command line version of 7-Zip for macOS was released.
- The speed for LZMA and LZMA2 decompression in arm64 versions for macOS and Linux 
  was increased by 20%-60%.
- Some changes and improvements in ZIP, TAR and NSIS code.

21.01 alpha    2021-03-09
-------------------------
- The command line version of 7-Zip for Linux was released.
- The improvements for speed of ARM64 version using hardware CPU instructions 
  for AES, CRC-32, SHA-1 and SHA-256.
- The bug in versions 18.02 - 21.00 was fixed:
  7-Zip could not correctly extract some ZIP archives created with xz compression method.
- Some bugs were fixed.

21.00 alpha    2021-01-19
-------------------------
- Some internal changes in code.
- Some bugs were fixed.
- New localizations: Tajik, Uzbek (Cyrillic)

20.02 alpha    2020-08-08
-------------------------
- The default number of LZMA2 chunks per solid block in 7z archive was increased to 64.
  It allows to increase the compression speed for big 7z archives, if there is a big number 
  of CPU cores and threads.
- The speed of PPMd compressing/decompressing was increased for 7z/ZIP/RAR archives.
- The new -ssp switch. If the switch -ssp is specified, 7-Zip doesn't allow the system 
  to modify "Last Access Time" property of source files for archiving and hashing operations. 
- Some bugs were fixed.
- New localization: Swahili.

20.00 alpha    2020-02-06
-------------------------
- 7-Zip now supports new optional match finders for LZMA/LZMA2 compression: bt5 and hc5, 
  that can work faster than bt4 and hc4 match finders for the data with big redundancy.
- The compression ratio was improved for Fast and Fastest compression levels with the 
  following default settings:
   - Fastest level (-mx1) : hc5 match finder with 256 KB dictionary.
   - Fast    level (-mx3) : hc5 match finder with 4 MB dictionary.
- Minor speed optimizations in multithreaded LZMA/LZMA2 compression for Normal/Maximum/Ultra 
  compression levels.
- bzip2 decoding code was updated to support bzip2 archives, created by lbzip2 program.
- Some bugs were fixed.
- New localization: Turkmen.

19.02 alpha    2019-09-05
-------------------------
- 7-Zip now can unpack files encoded with Base64 encoding (b64 filename extension).
- 7-Zip now can use new x86/x64 hardware instructions for SHA-1 and SHA-256, supported
  by AMD Ryzen and latest Intel CPUs: Ice Lake and Goldmont.
  It increases
    - the speed of SHA-1/SHA-256 hash value calculation, 
    - the speed of encryption/decryption in zip AES, 
    - the speed of key derivation for encryption/decryption in 7z/zip/rar archives.
- The speed of zip AES encryption and 7z/zip/rar AES decryption was increased with 
  the following improvements:
   - 7-Zip now can use new x86/x64 VAES (AVX Vector AES) instructions, supported by 
     Intel Ice Lake CPU. 
   - The existing code of x86/x64 AES-NI was improved also.
- There is 2% speed optimization in 7-Zip benchmark's decompression.
- Some bugs were fixed.

19.00          2019-02-21
-------------------------
- Encryption strength for 7z archives was increased:
  the size of random initialization vector was increased from 64-bit to 128-bit,
  and the pseudo-random number generator was improved.
- Some bugs were fixed.

18.06          2018-12-30
-------------------------
- The speed for LZMA/LZMA2 compressing was increased by 3-10%,
  and there are minor changes in compression ratio.
- Some bugs were fixed.
- The bug in 7-Zip 18.02-18.05 was fixed: there was memory leak in xz decoder.
- 7-Zip 18.02-18.05 used only one CPU thread for bz2 archive creation.

18.05          2018-04-30
-------------------------
- The speed for LZMA/LZMA2 compressing was increased 
    by 8% for fastest/fast compression levels and 
    by 3% for normal/maximum compression levels.
- 7-Zip now shows Properties (Info) window and CRC/SHA results window
  as "list view" window instead of "message box" window.
- Some improvements in zip, hfs and dmg code.
- Previous versions of 7-Zip could work incorrectly in "Large memory pages" mode in
  Windows 10 because of some BUG with "Large Pages" in Windows 10. 
  Now 7-Zip doesn't use "Large Pages" on Windows 10 up to revision 1709 (16299).
- The vulnerability in RAR unpacking code was fixed (CVE-2018-10115).
- Some bugs were fixed.

18.03 beta     2018-03-04
-------------------------
- The speed for single-thread LZMA/LZMA2 decoding
  was increased by 30% in x64 version and by 3% in x86 version.
- 7-Zip now can use multi-threading for 7z/LZMA2 decoding,
  if there are multiple independent data chunks in LZMA2 stream.
- 7-Zip now can use multi-threading for xz decoding,
  if there are multiple blocks in xz stream.
- New localization: Kabyle.
- Some bugs were fixed.

18.01          2018-01-28
-------------------------
- 7-Zip now can unpack DMG archives that use LZFSE compression method.
- 7-Zip now doesn't allow update operation for archives that have read-only attribute.
- The BUG was fixed:
  extracting from tar with -si switch didn't set timestamps for directories.
- Some bugs were fixed.

18.00 beta     2018-01-10
-------------------------
- 7-Zip now can unpack OBJ/COFF files.
- new -sse switch to stop archive creating, if 7-Zip can't open some input file. 
- Some bugs were fixed.

17.01 beta     2017-08-28
-------------------------
- Minor speed optimization for LZMA2 (xz and 7z) multi-threading compression.
  7-Zip now uses additional memory buffers for multi-block LZMA2 compression.
  CPU utilization was slightly improved.
- 7-zip now creates multi-block xz archives by default. Block size can be 
  specified with -ms[Size]{m|g} switch.
- xz decoder now can unpack random block from multi-block xz archives.
  7-Zip File Manager now can open nested multi-block xz archives 
  (for example, image.iso.xz) without full unpacking of xz archive.
- 7-Zip now can create zip archives from stdin to stdout.
- 7-Zip command line: @listfile now doesn't work after -- switch.
  Use -i@listfile before -- switch instead.
- The BUGs were fixed:
  7-Zip could add unrequired alternate file streams to WIM archives, 
  for commands that contain filename wildcards and -sns switch.
  7-Zip 17.00 beta crashed for commands that write anti-item to 7z archive.
  7-Zip 17.00 beta ignored "Use large memory pages" option.

17.00 beta     2017-04-29
-------------------------
- ZIP unpacking code was improved.
- 7-Zip now reserves file space before writing to file (for extraction from archive).
  It can reduce file fragmentation.
- Some bugs were fixed. 7-Zip could crash in some cases.
- Internal changes in code.

16.04          2016-10-04
-------------------------
- The bug was fixed: 7-Zip 16.03 exe installer under Vista didn't create 
  links in Start / Programs menu.
- Some bugs were fixed in RAR code.

16.03          2016-09-28
-------------------------
- Installer and SFX modules now use some protection against DLL preloading attack.
- Some bugs were fixed in 7z, NSIS, SquashFS, RAR5 and another code.

16.02          2016-05-21
-------------------------
- 7-Zip now can extract multivolume ZIP archives (z01, z02, ... , zip).
- Some bugs were fixed.

15.14          2015-12-31
-------------------------
- 7-Zip File Manager:
  - The code for "Open file from archive" operation was improved.
  - The code for "Tools/Options" window was improved.
  - The BUG was fixed: there was incorrect mouse cursor capture for 
    drag-and-drop operations from open archive to Explorer window.
- Some bugs were fixed.
- New localization: Yoruba.

15.12          2015-11-19
-------------------------
- The release version.

15.11 beta     2015-11-14
-------------------------
- Some bugs were fixed.

15.10 beta     2015-11-01
-------------------------
- The BUG in 9.21 - 15.09 was fixed:
  7-Zip could ignore some parameters, specified for archive creation operation
  for gzip and bzip2 formats in "Add to Archive" window and in command line 
  version (-m switch).
- Some bugs were fixed.

15.09 beta     2015-10-16
-------------------------
- 7-Zip now can extract ext2 and multivolume VMDK images.
- Some bugs were fixed.

15.08 beta     2015-10-01
-------------------------
- 7-Zip now can extract ext3 and ext4 (Linux file system) images.
- Some bugs were fixed.

15.07 beta     2015-09-17
-------------------------
- 7-Zip now can extract GPT images and single file QCOW2, VMDK, VDI images.
- 7-Zip now can extract solid WIM archives with LZMS compression.
- Some bugs were fixed.

15.06 beta     2015-08-09
-------------------------
- 7-Zip now can extract RAR5 archives.
- 7-Zip now doesn't sort files by type while adding to solid 7z archive.
- new -mqs switch to sort files by type while adding to solid 7z archive.
- The BUG in 7-Zip File Manager was fixed:
  The "Move" operation to open 7z archive didn't delete empty files.
- The BUG in 15.05 was fixed:
  console version added some text to the end of stdout stream, is -so switch was used. 
- The BUG in 9.30 - 15.05 was fixed:
  7-Zip could not open multivolume sfx RAR archive.
- Some bugs were fixed.

15.05 beta     2015-06-14
-------------------------
- 7-Zip now uses new installer.
- 7-Zip now can create 7z, xz and zip archives with 1536 MB dictionary for LZMA/LZMA2.
- 7-Zip File Manager now can operate with alternate file streams at NTFS
  volumes via "File / Alternate Streams" menu command.
- 7-Zip now can extract .zipx (WinZip) archives that use xz compression.
- new optional "section size" parameter for BCJ2 filter for compression ratio improving.
  Example: -mf=BCJ2:d9M, if largest executable section in files is smaller than 9 MB. 
- Speed optimizations for BCJ2 filter and SHA-1 and SHA-256 calculation.
- Console version now uses stderr stream for error messages.
- Console version now shows names of processed files only in progress line by default.
- new -bb[0-3] switch to set output log level. -bb1 shows names of processed files in log. 
- new -bs[o|e|p][0|1|2] switch to set stream for output messages;
      o: output, e: error, p: progress line; 0: disable, 1: stdout, 2: stderr.
- new -bt switch to show execution time statistics.
- new -myx[0-9] switch to set level of file analysis.
- new -mmtf- switch to set single thread mode for filters.
- The BUG was fixed:
  7-Zip didn't restore NTFS permissions for folders during extracting from WIM archives.
- The BUG was fixed:
  The command line version: if the command "rn" (Rename) was called with more 
  than one pair of paths, 7-Zip used only first rename pair.
- The BUG was fixed:
  7-Zip crashed for ZIP/LZMA/AES/AES-NI.
- The BUG in 15.01-15.02 was fixed:
  7-Zip created incorrect ZIP archives, if ZipCrypto encryption was used.
  7-Zip 9.20 can extract such incorrect ZIP archives.
- Some bugs were fixed.

9.38 beta      2015-01-03
-------------------------
- Some bugs were fixed.

9.36 beta      2014-12-26
-------------------------
- The BUG in command line version was fixed:
  7-Zip created temporary archive in current folder during update archive
  operation, if -w{Path} switch was not specified. 
  The fixed 7-Zip creates temporary archive in folder that contains updated archive.
- The BUG in 9.33-9.35 was fixed:
  7-Zip silently ignored file reading errors during 7z or gz archive creation,
  and the created archive contained only part of file that was read before error.
  The fixed 7-Zip stops archive creation and it reports about error.
- Some bugs were fixed.

9.35 beta      2014-12-07
-------------------------
- The BUG was fixed:
  7-Zip crashed during ZIP archive creation, if the number of CPU threads was more than 64.
- The BUG in 9.31-9.34 was fixed:
  7-Zip could not correctly extract ISO archives that are larger than 4 GiB.
- The BUG in 9.33-9.34 was fixed:
  The option "Compress shared files" and -ssw switch didn't work.
- The BUG in 9.26-9.34 was fixed:
  7-Zip File Manager could crash for some archives open in "Flat View" mode.
- Some bugs were fixed.

9.34 alpha     2014-06-22
-------------------------
- The BUG in 9.33 was fixed:
  Command line version of 7-Zip could work incorrectly, if there is relative 
  path in exclude filename optiton (-x) and absolute path as include filename.
- The BUG in 9.26-9.33 was fixed:
  7-Zip could not open some unusual 7z archives that were created by another 
  software (not by 7-Zip).
- The BUG in 9.31-9.33 was fixed:
  7-Zip could crash with switch -tcab.

9.33 alpha     2014-06-15
-------------------------
- 7-Zip now can show icons for 7-Zip items in Explorer's context menu. 
- "Add to archive" dialog box: 
    - new options in "Path Mode"
    - new option "Delete files after compression"
    - new "NTFS" options for WIM and TAR formats:
	- Store symbolic links
	- Store hard links
	- Store alternate data streams
	- Store file security
- "Extract" dialog box:
    - new optional field to set output folder name
    - new option "Eliminate duplication of root folder"
    - new option "Absolute pathnames" in "Path Mode".
    - new option "Restore file security" (that works for WIM archives only)
- 7-Zip File Manager:
    - new "File / Link" dialog box in to create  symbolic links and hard links.
- Command line version:
    - new -spd switch to Disable wildcard matching for file names
    - new -spe switch to Eliminate duplication of root folder for extract archive command
    - new -snh switch to store hard links as links (WIM and TAR formats only)
    - new -snl switch to store symbolic links as links (WIM and TAR formats only)
- NSIS support was improved. 
- The problem was fixed: 
    The command "extract to \*" with multiple archives could use same 
    output folder, if archives are placed inside PE (EXE) file.
- The BUG of 9.31-9.32 was fixed:
    Command line version for test and extract commands returned the 
    value 0 as exit code, if it couldn't open archive.
- The BUG was fixed:
    7-Zip could not create archives with anti-items for any archive type,
    except of 7z type
- Some bugs were fixed.
- New localization: Mongolian (script).

9.32 alpha     2013-12-01
-------------------------
- 7-Zip now can create multivolume SFX archives in 7z format.
  Standalone sfx module now can unpack external 7z archive with name that is
  matched to name of sfx module. For example, sfx module renamed to archive.exe 
  can unpack archive.7z or archive.7z.001 .
- ZIP, NSIS, HFS, AR support was improved.
- 7-Zip now supports files larger than 4 GiB in ISO archives.
- Improved compression ratio in 7z format with maximum or ultra level for
  executable files (EXE and DLL) that are larger than 16 MB (improved BCJ2 filter).
- Improved support for file pathnames longer than 260 characters.
- CRC and SHA checksum calculation for files can be called via Explorer's context menu.
- 7-Zip File Manager now also takes into account the numbers in filenames for sorting order.
- 7-Zip File Manager now can use RAM buffers instead of temp files to open 
  nested archives, if temp file is smaller than 1/4 of RAM size.
- 7-Zip File Manager can open files in "Parser" mode via "Open Archive > #" context 
  menu command. It shows the list of archives inside file.
- Command line version:
    - new -t# switch to open file in "Parser" mode and show the list of archives inside file.
    - new -stx{Type} switch to exclude archive type from using.
    - -scs switch now supports UTF-16 encoding.
    - now it shows time and memory usage statistics at the end of execution.
- The BUGs were fixed:
    - 7-Zip 9.30 and early versions created ZIP archives with minor errors
      in extra field of headers for directory items, if AES (WinZip-AES) encryption was used.
    - 7-Zip could work incorrectly in decompression of more than one 
      multi-volume archive in one command.
    - 7-Zip 9.24 alpha - 9.30 alpha versions could not extract ZIP archives 
      encrypted with PKWARE-AES method.
- Minimum supported system now is Windows 2000. 7-Zip doesn't work on Windows 95/98/ME.
- New localization: Irish.

9.30 alpha     2012-10-26
-------------------------
- LZMA2 now is default compression method for .7z format.
- 7-Zip now can update WIM archives.
- 7-Zip File Manager now can move files to archives.
- The default encoding for TAR format now is UTF-8. You can use -mcp=1 switch for OEM encoding.
- Command line version:
    - new "rn" command to rename files in archive.
    - new -sdel switch to delete files after including to archive.
    - new -sns switch to store NTFS alternate streams (for WIM format only). 
    - new -sni switch to store NT security information for files (for WIM format only).
    - new -stl switch to set archive timestamp from the most recently modified file.
- Speed optimizations for opening big archives and big disk folders.
- 7-Zip now writes special padding blocks to headers of 7z archives for 
  faster archive opening. Note that 7-Zip 4.50 - 4.58 contain BUG, 
  so these old versions can't correctly work with such new 7z archives.
- DMG support was improved
- Some bugs were fixed.
- The BUG in 7-Zip 9.26 alpha - 9.29 alpha versions was fixed.
  These alpha versions could not open non-solid 7z archive, if 
  some files were skipped during creation of that archive.
  That problem is also related to 7z archives created in solid mode,
  if each solid block contains no more than one file.
  Note: 7-Zip skips files that were open for writing by another 
  application and shows warning in that case.
- New localization: Aragonese.

9.25 alpha     2011-09-16
-------------------------
- LZMA decompression speed was improved.
- "compress and send to email" code was improved to support more email clients.
- New command "h" to calculate hash values CRC-32, CRC-64, SHA-256 or SHA-1 for files on disk.
- New -spf switch to store full file paths including drive letter to archive.
  If you use that switch with extract command, please check that file names in archive are correct.
- Some bugs were fixed.

9.23 alpha     2011-06-07
-------------------------
- The format of language files was changed.
- Some bugs were fixed.
- New localization: Karakalpak.

9.22 beta      2011-04-18
-------------------------

- 7-Zip now uses progress indicator displayed on a taskbar button under Windows 7.
- The BUG in 7-Zip 9.21 beta was fixed: 
    7-Zip could ignore some options when you created ZIP archives.
    For example, it could use ZipCrypto cipher instead of AES-256.

9.21 beta      2011-04-11
-------------------------
- 7-Zip now can unpack UEFI BIOS files.
- 64-bit version of 7-Zip now includes additional 32-bit shell extension DLL.
  So other 32-bit programs can call 64-bit 7-Zip via context menu.
- Now it's possible to associate 7-Zip with file types without Administrator rights.
- New -mf=FilterID switch to specify compression filter. Examples:
    7z a -mf=bcj2 a.7z a.tar 
    7z a -mf=delta:4 a.7z a.wav 
    7z a -mf=bcj a.tar.xz a.tar 
- 32-bit 7-Zip running under 64-bit Windows now can use up to 4 GB of RAM.
- Some bugs were fixed.
- New localizations: Corsican, Kyrgyz, Ligurian.

9.20           2010-11-18
-------------------------
- Some bugs were fixed.

9.19 beta      2010-11-11
-------------------------
- The console version now doesn't show entered password.
- Some bugs were fixed.

9.18 beta      2010-11-02
-------------------------
- 7-Zip now can unpack SquashFS and CramFS filesystem images.
- 7-Zip now can unpack some TAR and ISO archives with incorrect headers.
- New small SFX module for installers (in Extra package).
- Some bugs were fixed.

9.17 beta      2010-10-04
-------------------------
- Disk fragmentation problem for ZIP archives created by 7-Zip was fixed.

9.16 beta      2010-09-08
-------------------------
- 7-Zip now supports files that are larger than 8 GB in TAR archives.
- NSIS support was improved.
- Some bugs were fixed.
- New localizations: Hindi, Gujarati, Sanskrit.

9.15 beta      2010-06-20
-------------------------
- Some bugs were fixed.
- New localization: Tatar.

9.14 beta      2010-06-04
-------------------------
- WIM support was improved.

9.13 beta      2010-04-15
-------------------------
- 7-Zip now stores NTFS file timestamps to ZIP archives.
- New additional "Open archive >" item in context menu allows to select 
  archive type for some files.
- Some bugs were fixed.
- New localization: Uyghur.

9.12 beta      2010-03-24
-------------------------
- ZIP / PPMd compression ratio was improved in Maximum and Ultra modes.
- The BUG in 7-Zip 9.* beta was fixed: LZMA2 codec didn't work,
  if more than 10 threads were used (or more than 20 threads in some modes).

9.11 beta      2010-03-15
-------------------------
- 7-Zip now supports PPMd compression in ZIP archives.
- Speed optimizations in PPMd codec.
- The support for archives in installers was improved.
- Some bugs were fixed.
- New localization: Kazakh.

9.10 beta      2009-12-22
-------------------------
- The BUG in 7-Zip 9.09 beta was fixed:
    7-Zip created incorrect ZIP archives, if ZipCrypto encryption was used.

9.09 beta      2009-12-12
-------------------------
- 7-Zip now can unpack Apple Partition Map (APM) disk images.
- Speed optimizations in AES code for Intel's 32nm CPUs.
- Speed optimizations in CRC calculation code for Intel's Atom CPUs.
- Some bugs were fixed.

9.07 beta      2009-08-27
-------------------------
- It's possible to specify Diff program in options (7-Zip File Manager).
- Some bugs were fixed.

9.06 beta      2009-08-17
-------------------------
- 7-Zip now can unpack MSLZ archives.
- Partial parsing for EXE resources, SWF and FLV.
- Some bugs were fixed.

9.04 beta      2009-05-30
-------------------------
- 7-Zip now can update solid .7z archives.
- 7-Zip now supports LZMA2 compression method.
- 7-Zip now supports XZ archives.
- 7-Zip now can unpack NTFS, FAT, VHD and MBR archives.
- 7-Zip now can unpack GZip, BZip2, LZMA, XZ and TAR archives from stdin.
- 7-Zip now can open/copy/compress disk images (like \\.\c:) from \\.\ folder.
- 7-Zip File Manager now doesn't use temp files to open nested archives 
  stored without compression.
- New -scrc switch to calculate total CRC-32 during extracting / testing.
- New -scc{WIN|DOS|UTF-8} switch to specify charset for console input/output (default = DOS).
- Some bugs were fixed.

4.65           2009-02-03
-------------------------
- 7-Zip File Manager now can calculate SHA-256 checksum.
- Some bugs were fixed.

4.64           2009-01-03
-------------------------
- The bug in 7-Zip 4.63 was fixed: 7-Zip could not decrypt .ZIP archives 
  encrypted with WinZip-AES method.

4.63           2008-12-31
-------------------------
- 7-Zip now can unpack ZIP archives encrypted with PKWARE-AES.
- Some bugs were fixed.

4.62           2008-12-02
-------------------------
- Some bugs were fixed.

4.61 beta      2008-11-23
-------------------------
- 7-Zip now supports LZMA compression for .ZIP archives.
- Some bugs were fixed.
- New localization: Sinhala.

4.60 beta      2008-08-19
-------------------------
- Some bugs were fixed.

4.59 beta      2008-08-13
-------------------------
- 7-Zip now can unpack UDF, XAR and DMG/HFS archives.
- 7-Zip File Manager now keeps encryption when you edit encrypted file inside archive.
- 7-Zip File Manager now allows to change current folder from the address bar drop-down list.
- It's allowed to use -t switch for "list" and "extract" commands.
- Some bugs were fixed.
- New localizations: Icelandic, Kurdish Sorani.

4.58 beta      2008-05-05
-------------------------
- Some speed optimizations.
- 7-Zip now can unpack .lzma archives.
- Unicode (UTF-8) support for filenames in .ZIP archives. Now there are 3 modes:
    1) Default mode: 7-Zip uses UTF-8, if the local code page doesn't contain required symbols.
    2) -mcu switch:  7-Zip uses UTF-8, if there are non-ASCII symbols.
    3) -mcl switch:  7-Zip uses local code page.
- Now it's possible to store file creation time in 7z and ZIP archives (-mtc switch).
- 7-Zip now can unpack multivolume RAR archives created with 
  "old style volume names" scheme and names *.001, *.002, ...
- Now it's possible to use -mSW- and -mSW+ switches instead of -mSW=off and -mSW=on  
- Some bugs were fixed.
- New localizations: Punjabi (Indian), Pashto.

4.57           2007-12-06
-------------------------
- The BUG in command line version was fixed: -up3 switch 
  could work incorrectly.

4.56 beta      2007-10-24
-------------------------
- Some bugs were fixed.

4.55 beta      2007-09-05
-------------------------
- Some bugs were fixed.

4.54 beta      2007-09-04
-------------------------
- Decompression speed was increased.

4.53 beta      2007-08-27
-------------------------
- "Test" and "Info" buttons now work for open archives.
- The bug in 7-Zip 4.48 - 4.52 beta was fixed:
    7-Zip could create .ZIP archives with broken files.
- Some bugs were fixed.

4.52 beta      2007-08-03
-------------------------
- 7-Zip now can unpack Compound files (msi, doc, ...).
- Some bugs were fixed.

4.51 beta      2007-07-25
-------------------------
- Bug was fixed: 7-Zip 4.50 beta could not open some .7z archives.

4.50 beta      2007-07-24
-------------------------
- New switch for command line version:
    -ssc[-] enables/disables case-sensitive mode for file names.
- Speed optimizations for AES encryption.
- Some bugs were fixed.

4.49 beta      2007-07-11
-------------------------
- 7-Zip now can unpack WIM archives.
- 7-Zip now replaces incorrect characters in filenames during extracting.

4.48 beta      2007-06-26
-------------------------
- Encryption strength for .7z format was increased. 
  Now it uses random initialization vectors.
- Some bugs were fixed.

4.47 beta      2007-05-27
-------------------------
- Bugs of 7-Zip 4.46 beta were fixed: BZip2 could work incorrectly.

4.46 beta      2007-05-25
-------------------------
- New fast compression mode for Deflate method in Zip and GZip.
- New "Compress shared files" option in GUI and -ssw switch.
- Some bugs were fixed.
- New localization: Norwegian Nynorsk.

4.45 beta      2007-04-17
-------------------------
- Now it's possible to specify the size of solid block and the number 
  of CPU threads in "Add to archive" dialog box. 
- Default dictionary size was increased: Normal: 16 MB, Max: 32 MB.
- Speed optimizations.
- Benchmark was improved (new "b" command in command line version).
- The number of DLL files was reduced.
- Now it's possible to associate 7-zip with combined types like .tbz2
- switch -mhcf=off is not supported now.
- If -t{Type} switch is not specified, 7-Zip now uses extension of archive to 
  detect the type of archive.
- Some bugs were fixed.
- New localization: Welsh.

4.44 beta      2007-01-20
-------------------------
- Speed optimizations for LZMA, Deflate, BZip2 and unRAR.
- 7-Zip now supports file pathnames longer than 260 characters.
- Some bugs were fixed.
- New localizations: Bangla, Bashkir, Nepali.

4.43 beta      2006-09-15
-------------------------
- 7-Zip now can use multi-threading mode for compressing to .ZIP archives.
- ZIP format supporting was improved.
- 7-Zip now supports WinZip-compatible AES-256 encryption for .ZIP archives.
- New context menu items for .ZIP archives creating.
- 7-Zip now uses order list (list of extensions) for files sorting for compressing 
  to .7z archives. It can slightly increase compression ratio in some cases.
- 7-Zip now restores modification time of folders during .7z archives extracting.
- Some bugs were fixed.
- New localizations: Armenian, Marathi.

4.42           2006-05-14
-------------------------
- Compressing speed and Memory requirements were increased.
  Default dictionary size was increased: Fastest: 64 KB, Fast: 1 MB, 
  Normal: 4 MB, Max: 16 MB, Ultra: 64 MB.
- BZip2 compressing / decompressing now can work in multi-threading mode
- Multi-threading mode now is default for multi-processor systems
- 64-bit version now supports 1 GB dictionary
- 7z/LZMA now can use only these match finders: HC4, BT2, BT3, BT4
- Compression ratio in Zip/GZip/Deflate in Ultra mode was increased
- 7-Zip now can unpack ISO archives and some installers created by NSIS
- Optional "Flat View" mode in 7-Zip File Manager
- 7-Zip File Manager now can calculate CRC checksums for files
- -x switch with relative paths now affects files specified with absolute paths
- New switch for 7za.exe (console version): -slt.
  "l" (list) command with -slt shows technical information for archive.
- New switch: -scs{WIN|DOS|UTF-8} specifies charset for list files.
  Default charset for list files is UTF-8 now.
- Some bugs were fixed
- New localizations: Albanian, Kurdish

4.32           2005-12-09
-------------------------
- Bug was fixed: 7-Zip 4.31 didn't work in Windows 95

4.31           2005-12-04
-------------------------
- Small changes
- New localization: Basque

4.30 beta      2005-11-18
-------------------------
- Files 7zFMn.exe, 7zGn.exe, 7-zipn, 7za.exe, 7zC.sfx were removed from 7-zip package
- 7-Zip now uses uncompressed SFX: 7z.sfx
- Sfx modules 7z.sfx and 7zCon.sfx now use msvcrt.dll
- Speed optimizations in LZMA maximum/ultra compressing.
- LZMA now supports word size up to 273
- 7-Zip now reduces dictionary size for LZMA, if you compress files 
  smaller than specified dictionary size.
- 7-Zip now can use large memory pages:
    GUI: 7-Zip File Manager / Options / Settings / Use large memory pages.
    Command line version: -slp switch.
  This feature allows to increase speed of compressing.
  But 7-Zip can make some pause at starting of compressing for allocating large pages.
  Also Task Manager doesn't show real memory usage of program, if 7-Zip uses large pages.
  This feature works only on Windows 2003 / XP x64 / Vista. 
  Also you must have administrator's rights for your system.
  Recommended size of RAM: 1 GB or more.
  To install this feature you must run 7-Zip File Manager at least once, 
  close it and reboot system.
- Some bugs were fixed

4.29 beta      2005-09-28
-------------------------
- Bug was fixed: 7-Zip 4.28 beta worked incorrectly in Windows 95/98/Me

4.28 beta      2005-09-27
-------------------------
- Bug was fixed: 7-Zip 4.27 beta created incorrect multivolume archives.
- "Duplicate filename" collision problem between names with ligatures was fixed.

4.27 beta      2005-09-21
-------------------------
- 7-Zip can unpack CHM/HXS (MS HTML HELP) archives
- 7-Zip can unpack multivolume CAB archives
- Now 7-Zip deletes files to the Recycle Bin by default.
  Shift+Delete deletes files permanently.
- Some bugs were fixed
- New localization: Tatarish

4.26 beta      2005-08-05
-------------------------
- LZH format support (extracting only)
- Some bugs were fixed
- New localization: Ido

4.25 beta      2005-07-31
-------------------------
- 7-Zip now doesn't interrupt the compressing when it can not 
  find specified file as in version 4.24 beta. It just shows warning.
- 7-Zip now supports standard selection mode in the file list
- Some bugs were fixed

4.24 beta      2005-07-06
-------------------------
- 7-Zip now supports right-click Drag and Drop in Explorer
- Command line version now supports short file names (like FILENA~1.TXT)
- If there are no wildcard names and there is no -r switch in command line, 
  7-Zip now checks that specified files exist on disk before compressing.
- Some bugs were fixed

4.23           2005-06-29
-------------------------
- Drag and Drop support
- 7-Zip File Manager now can copy files from one archive to another
- Some bugs were fixed
- New localizations: Extremaduran, Malay

4.20           2005-05-30
-------------------------
- No changes 

4.19 beta      2005-05-21
-------------------------
- BZip2 code was rewritten. Now it supports 3 modes: Normal, Maximum and 
  Ultra. In Normal mode it compresses almost as original BZip2 compressor. 
  Compression ratio in Maximum and Ultra modes is 1-3% better for some files, 
  but Maximum Mode is about 3 times slower and Ultra Mode is about 8 times 
  slower than Normal mode.
- Console version now prints all messages to stdout by default,
  and if -so switch is specified, 7-Zip prints messages to stderr.
- Some bugs were fixed
- New localizations: Azeri, Georgian

4.18 beta      2005-04-19
-------------------------
- Bug in v4.17 beta was fixed: 7-Zip File Manager could crash 
  after some operations with archives

4.17 beta      2005-04-18
-------------------------
- To increase protection from viruses, 7-Zip now does not open 
  files with more than 4 continuous spaces in the name. 
  And 7-Zip changes such long spaces in name to " ... " in the file list.
- Code size optimization
- Some files were moved from main package to extra package:
    - Plugin for FAR Manager
    - SFX modules for installers (7zS.sfx and 7zSD.sfx)
- New localizations: Asturian, Indonesian

4.16 beta      2005-03-29
-------------------------
- Speed optimization (5%) for 7z / LZMA 
- 7za.exe now supports .Z archives
- -r- switch in command line now is default for all commands 
- Some bugs were fixed
- New localization: Uzbek

4.15 beta      2005-01-25
-------------------------
- Z format supporting (extracting only)
- 7-Zip now can extract ZIP archives compressed with "Shrink" method
- 7-Zip now doesn't interrupt the compressing when it can not open file.
  7-Zip just skips that file and shows warning.
- Some bugs were fixed
- New localization: Frisian

4.14 beta      2005-01-11
-------------------------
- 7-Zip installer was created with NSIS.
  Now it installs 7-Zip for all users (under Windows 2000/XP).
- Now 7-Zip can create multivolume archives
  (switch -v for command line)
- Some bugs were fixed
- New localizations: Breton, Farsi

4.13 beta      2004-12-14
-------------------------
- Switch "--" stops switches parsing
- Some bugs were fixed

4.12 beta      2004-11-18
-------------------------
- Bug in v4.11 beta was fixed:
    7-Zip created incorrect ZIP archives if file size was 
    from 3.75 GB to 4 GB.

4.11 beta      2004-11-16
-------------------------
- 7-Zip now shows file names during compressing/decompressing
- 7-Zip now supports Zip64 extension of ZIP format. So now it's 
  possible to compress files bigger than 4 GB to ZIP archives.
- Some bugs were fixed
- New localization: Galician

4.10 beta      2004-10-21
-------------------------
- Bugs in v4.0* were fixed:
  - Some commands in command line with "-r" switch worked incorrectly,
    so 7-zip could skip some files during compressing
  - Some other bugs were fixed
- Small internal changes

4.09 beta      2004-10-05
-------------------------
- Bugs in v4.0* were fixed:
  - Renaming inside archives didn't work or worked incorrectly
  - GUI SFX didn't show extracting dialog at start
- Small fixes in 7-Zip GUI (7zG.exe)

4.08 beta      2004-10-04
-------------------------
- Bug in installer for v4.07 was fixed: when rebooting 
  is required, it rebooted without asking user
- Small fixes in 7-Zip GUI (7zG.exe)

4.07 beta      2004-10-03
-------------------------
- Big amount of code was changed in this beta version.
  So don't use it for important data compressing. 
  And test archive after compressing.

- Unified command line interface to GUI and console versions
- 7-Zip now can extract or test several archives in one command  
- 7-Zip now doesn't interrupt the compressing when file is locked by 
  other application. 7-Zip just skips that file and shows warning.
  Note: previous versions of 7-Zip had bug, so they can not unpack 
  non-solid and some solid 7z archives with such skipped files.
- Command line interface was changed:
    - now it's possible to use absolute pathnames
    - syntax simplification:
        was: 7z a a Folder1\* Folder2\* -r
        now: 7z a a Folder1 Folder2
    - now it's possible to use complex wildcard commands, like *\*111*\*
- More smart detection of archive type for files with unusual
  file name extensions
- Supporting for RAR archives with encrypted headers
- CPIO format supporting was improved
- For GZip and BZip2 formats you can:
    - Compress from stdin (-si switch)
    - Compress to stdout (-so switch)
    - Extract to stdout (-so switch)
- 7-Zip File Manager:
  - Split and Combine commands
  - new list view options: Full row select, Show grid lines
- Internal reconstruction
- Some bugs were fixed
- New localizations: Friulian, Macedonian, Mongolian, Tamil, Thai

3.13           2003-12-11
-------------------------
- Some small bugs were fixed

3.12           2003-12-10
-------------------------
- Now you can select compression method, dictionary size
  and word size in "Add to archive" dialog box. Also it 
  shows memory usage.
- 7-Zip File Manager now contains toolbars.
- New "Benchmark" command in 7-Zip File Manager.
  It measures compressing and decompressing speeds and 
  shows rating values.
- Some bugs were fixed.

3.11           2003-10-06
-------------------------
- 7-zip now use limitations for solid block size
  for increasing the speed of random file decompressing:
    - in Store mode:     0  B
    - in Fast mode:     16 MB
    - in Normal mode:  256 MB
    - in Maximum mode:   1 GB 
    - in Ultra mode:     4 GB 
- 7z.exe, 7za.exe and SFX modules now support Unicode 
  file names under Windows NT/2000/XP/2003.
  7zn.exe and 7zan.exe were removed from package. 
- Some bugs were fixed
- New localization: Afrikaans

3.10           2003-09-27
-------------------------
- Drag-and-Drop from external application
- GUI version (7zG.exe) can compress files with absolute paths
- Compression dialog doesn't suggest bzip2 and gzip2 types when 
  there are more than one selected file
- Optional auto renaming for existing files during extraction 
  in command line version (-aot switch).
- Some bugs were fixed

3.09.02        2003-09-20
-------------------------
- Optional limitation for solid block size for increasing 
  the speed of random file decompressing (-ms switch)

3.09.01 beta   2003-09-06
-------------------------
- Automatic compression filter for executable files:
  dll, exe, ocx, sfx, sys, (-mf switch)
- Compression levels in 7z now are:
    - Fast:    32 KB dictionary, BCJ filter
    - Normal:   2 MB dictionary, BCJ filter
    - Maximum:  8 MB dictionary, BCJ filter, max settings
    - Ultra:   32 MB dictionary, BCJ2 filter, max settings
- Updating solid 7z archives now is supported, if it doesn't 
  require repacking solid blocks
- -mhcf switch for 7z format now is default
- Some bugs were fixed

3.08.04 beta   2003-08-24
-------------------------
- Favorites menu in 7-Zip File Manager
- Some bugs were fixed

3.08.03 beta   2003-08-21
-------------------------
- Automatic adding of extension to archive name in Compress Dialog
- Some bugs in previous 3.08.* versions were fixed:
    - Storing columns width inside archives in File Manager
    - Opening archive inside archive
    - Quotes in list files in console version

3.08.02 beta   2003-08-20
-------------------------
- Some bugs were fixed

3.08 beta      2003-08-19
-------------------------
- Compress dialog:
   - Supporting fast compressing mode (-mx=1 switch)
   - Multi-threading option for Multi-Processor systems 
     or Pentium 4 with Hyper-Threading
   - Encrypt file names option
- New context menu items:
   - Extract here
   - Extract to <Folder>
   - Compress and email
- Internal reconstruction, registry using was reduced
- New localization: Esperanto

2.30 Beta 32   2003-05-15
-------------------------
- New features in compressing / decompressing window.
- "Show password" option.
- Some other small changes.
- New localization: Valencian.

2.30 Beta 31   2003-04-29
-------------------------
- Some bugs were fixed.

2.30 Beta 30   2003-04-19
-------------------------
- 7-Zip File Manager:
   - Showing .. item.
   - 1/2 Panels mode switching (F9).
- Supporting Bzip2 compression in ZIP archives.
- Some bugs were fixed.
- Some optimization recompiling for reducing code size.

2.30 Beta 29   2003-04-07
-------------------------
- 7-Zip File Manager:
   - "7-Zip" and "System" submenus in "Files" menu.
   - Path history and "Browse" button in "Copy" dialog.
- RAR supporting was improved.
- Some bugs were fixed.
- Small changes in LZMA code.
- New localizations: Hebrew, Vietnamese.

2.30 Beta 28   2003-02-16
-------------------------
- Some bugs were fixed:
   - Updating 7z archives that are larger than 4 GB.
   - Using anti-items in 7z format.
   - Compressing empty files with password to zip format.
- In max mode 7z now uses 8 MB dictionary instead of 4 MB.
- 7-Zip File Manager:
   - Supporting file comments: Ctrl-Z.
   - New key alias for folder bookmarks: [Shift]+Alt+Number.

2.30 Beta 27   2003-01-24
-------------------------
- Two BUGs in two previous beta versions (Beta 25 and Beta 26) 
  were fixed:
    1. Incorrect compressing to non-solid 7z archive
       when files have some very big sizes:
       4 GB, 8 GB, 12 GB, 16 GB, ... 
    2. Incorrect percent showing in 7z compressing
       when files are bigger than 4 GB.
- Supporting multivolume RAR and SPLIT archives. 
- Supporting DEB archives.
- Supporting old version of CPIO format.
- Some bugs were fixed.
- New localizations: Korean, Swedish.

2.30 Beta 26   2003-01-12
-------------------------
- Supporting Deflate64 method in Zip archives.
- Supporting Rar 1.50 archives.
- Some bugs were fixed.

2.30 Beta 25   2003-01-02
-------------------------
- Encryption feature for 7z format (AES-256).
- New optional archive header compressing mode (-mhcf).
- Archive headers now always are compressed with LZMA method.
- Updating non-solid 7z archives without -ms=off now is allowed.
- Folder creating and item renaming inside archive now is supported.
- Supporting encrypted Rar3 archives.
- Supporting Unicode names in Rar3 archives.
- Some bugs were fixed.
- New localizations: Lithuanian, Voro.

2.30 Beta 24   2002-11-01
-------------------------
- Some internal reconstructions.
- -m switch syntax was slightly changed.
- Some bugs were fixed.
- New localizations: Catalan, Norwegian, Romanian.

2.30 Beta 23   2002-09-07
-------------------------
- Encryption feature for zip format.
- Percent indicating for some operations.
- Some bugs were fixed.

2.30 Beta 22   2002-08-31
-------------------------
- New program: 7-Zip File Manager.
- Command line version now doesn't allow absolute paths
  for compressing files.
- New localizations: Belarusian, Greek.
- Bug in FAR plugin was fixed:
    Incorrect updating when archive has no explicit 
    directory items for file items.
- Some bugs were fixed.

2.30 Beta 21   2002-07-08
-------------------------
- RAM requirements for LZMA (7z) compression were reduced.
- Small bug in FAR plugin was fixed.

2.30 Beta 20   2002-07-01
-------------------------
- RAM requirements for LZMA (7z) decompression were reduced.
- New localization: Turkish.
- Some bugs were fixed.

2.30 Beta 19   2002-04-11
-------------------------
- Supporting RAR 3.0 archives.
- New localizations: Danish, Ukrainian.

2.30 Beta 18   2002-03-25
-------------------------
- Compressing speed in 7z format was slightly increased.
- New localizations: Estonian, Finnish.
- Some bugs were fixed.

2.30 Beta 17   2002-03-03
-------------------------
- Supporting ARJ archives.
- New localization: Chinese Simplified.

2.30 Beta 16   2002-02-24
-------------------------
- Supporting RPM and CPIO archives.
- New fast compression mode for LZMA: -m0a=0.
- New match finders for LZMA: bt4b, hc3, hc4.
- Some bugs were fixed.

2.30 Beta 15   2002-02-17
-------------------------
- Compression ratio in 7z was slightly improved.
- New localization: Dutch.

2.30 Beta 14   2002-02-10
-------------------------
- Speed optimization for multiprocessor computers (-mmt switch).
- New localizations: Czech, Japanese, Polish.
- Some bugs were fixed.

2.30 Beta 13   2002-01-31
-------------------------
- New SFX module for installers.
- New match finder for LZMA: bt3.
- New localizations: Portuguese, Portuguese Brazil, Serbo-Croatian.
- Some bugs were fixed.

2.30 Beta 12   2002-01-16
-------------------------
- Bug was fixed: memory leak in Beta 11.
- New localization: Hungarian.

2.30 Beta 11   2002-01-15
-------------------------
- Archive testing feature for GUI version.
- Now 7-Zip can use more than 256 MB of RAM in all Windows versions.
- New localizations: Bulgarian, Chinese Traditional, Latvian, Slovak.
- Some bugs were fixed.

2.30 Beta 10   2002-01-11
-------------------------
- Bugs were fixed:
    - Updating 7z archives in Beta 8 and 9 didn't work.
    - Unicode version in Beta 9 didn't work in Windows NT4.
    - Some other bugs were fixed.
- New localizations: Arabic, French, Italian, Slovenian, Spanish.

2.30 Beta 9    2002-01-08
-------------------------
- Program localization: English, German, Russian.
- Additional optimized versions of programs 
  for Windows NT4/2000/XP.
- Two new match finders for LZMA: pat3h and pat4h.
- Some bugs were fixed.

2.30 Beta 8    2001-12-21
-------------------------
- 7-Zip now supports some zip archives that were not 
  supported by previous versions.
- 7-Zip now supports new state (-uw switch) for cases
  when 7-Zip can not detect whether file is newer or the same.
- Supporting anti-items in 7z format for incremental 
  update (-u with action #3).
- Some bugs were fixed.

2.30 Beta 7    2001-11-04
-------------------------
- BCJ2: new converter for x86 code.
- Supporting tar archives with very long file names
  (GNU extension to 'tar' format).
- Supporting multistream coders in 7z (-mb switch).
- More compressing parameters for zip and gzip 
  in console version (-m switch).
- Solid compressing option in Windows version.
- Compressing parameters option in Windows version.
- Auto renaming existing files feature for 
  extracting files.
- Overwrite mode switch for extracting (-ao).
- Some bugs were fixed.

2.30 Beta 6    2001-10-13
-------------------------
- Supporting 7z format in MultiArc plugin for FAR Manager.
- Some bugs were fixed.

2.30 Beta 5    2001-10-02
-------------------------
- Creating SFX archives from explorer.
- 7zWin.sfx: Windows version of SFX module.
- Auto adding .exe extension to SFX archive name.
- 7za.exe now supports 7z, bzip2, gzip, tar, zip.
- Some bugs were fixed.

2.30 Beta 4    2001-09-15
-------------------------
- Self extract capability for 7z format.
- 7z archive format is default for 7z.exe and 7za.exe.
- 7z in default mode now uses bt234 match finder
  and solid compression.
- 7z in maximum mode (-mx) now uses 4MB dictionary.

2.30 Beta 3    2001-09-10
-------------------------
- Bug was fixed: decompressing .7z solid archives 
  containing empty files.
- new 7za.exe: standalone command line version 
  (only for 7z format).
- Speed of compressing to Deflate format (zip, gzip) 
  was slightly increased.

2.30 Beta 2    2001-08-30
-------------------------
- Supporting the new 7z format with high compression ratio.
- -bd (Disable percentage indicator) switch in 
  console version.
- Bug in console version was fixed: 
    previous versions incorrectly execute compression 
    commands with non-recursive wildcards in combination 
    with subfolders.
- Some other bugs were fixed.

2.30 Beta 1    2001-05-07
-------------------------
- Speed of reading of archive contents was increased.
- Bug was fixed: incorrect showing file names with 
  national charsets in some zip archives.
- Now it is possible to compress files larger than 4GB 
  to GZip archives.

2.24           2001-03-21
-------------------------
- Bugs in GZip and Cab decoders were fixed.

2.23           2001-03-04
-------------------------
- Opening archive items in Explorer.
- Context menu for archive items in Explorer.
- Automatic adding extension to archive name in console version.
- Some bugs were fixed.

2.22           2001-01-21
-------------------------
- Supporting Zip archives containing more than 65535 files.
- Speed of Plugin for Explorer was increased.
- Searching start position of archive now is limited by 
  first 1MB part of file.
- Some bugs were fixed.
- Packet now doesn't contain 7zip.exe, far7zip.reg and 
  far7zip2.reg files. There is new far7z.reg file.

2.21           2000-12-21
-------------------------
- FAR Plugin was improved:

    - Showing process box during opening archives.
    - Viewing properties of file by Ctrl-A.
    - Alt-F6 in archive now immediately extracts selected files 
      to current directory.
      
- Some bugs were fixed:
    
    - Entering to archive's subfolders in Explorer by clicking 
      items in main window didn't work under Windows ME/2000.
    - Decompressing solid Rar archives sometimes gave error.
    - Console version 7z.exe during list operation incorrectly 
      showed file names with national (non-english) charsets.
    - FAR Plugin didn't execute some operations.
    - Showing percents during extracting ZIP archives sometimes 
      was incorrect.

2.20           2000-11-20
-------------------------
- Supporting BZip2 and Cab.
- New program architecture with external
  compression and cryptographic modules.
- Decryption support (Rar and Zip). 
- New console client. 
- Some bugs were fixed.

2.11           2000-06-15
-------------------------
- Bugs were fixed:

    - FAR Plugin incorrectly processed
      names of subdirectories that use national
      (non-english) charsets.
    - gzip plugin could not compress empty files.

2.10           2000-05-16
-------------------------
- First level 7-Zip Plugin for FAR Manager.
- GUI version with integration to Windows Shell.
- Compression and decompressing GZip and TAR formats.
- Decompression RAR.
- Install & Uninstall support.
- Some bugs were fixed.

2.01           1999-09-19
-------------------------
- Small bug was fixed.
- Compression ratio was improved for some files.

2.00           1999-07-18
-------------------------
- Release.
- Big bug was fixed: previous versions incorrectly worked
    during compressing with files that were referred by
    direct(without wildcards) paths, containing subdirs parts.
- Compression and decompression speed were improved.
- -mx switch (maXimize compression) was added.
- Small bugs were fixed.

2.00 Beta 1    1999-01-02
-------------------------
- Original beta version.

End of document

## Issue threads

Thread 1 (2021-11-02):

Any thought on releasing your wiring image files?

zcohenld, 2021-11-02:
Hey GadgetAngel,
First off, you're build log is impressively detailed. Its been super interesting reading through it.
I was looking at your wiring harness image and found it extremely helpful. I'm planning on making my own version of it just to help me out. I was wondering if you're willing to release an editable version of it? If made in Adobe software either an editable PDF or the Adobe file itself.
If not, I totally understand. I'm going to make my own regardless and give you credit (along with Thomas White), but just thought I'd ask before I start.
Thanks!
Zac

GadgetAngel, 2021-11-02:
Sure I can add the Wiring harness Photoshop file to my gitHub. I need to see if GitHub will accept the file.  I will be releasing a wiring diagram (functional and actual) once I get my "Litter Box" mod done.  I am adding a box on the back of the Voron 2.4 printer so I can have more space for all the PSU and electronics.  The Box's support brackets are giving me a hard time.  I will be posting more about this on my Build Log after I get the "Litter Box" design done.

Give me a day or two to get the wiring harness file up gitHub. I will put it in a sub directory called "Adobe" under the "Hiring Harness" directory.

zcohenld, 2021-11-03:
Thank you so much! I really appreciate it!
Not sure if you're aware but the Octopus image is killing your file size. I'm converting the PSD to Illustrator just because thats what I mainly use. Deleting just that one image dropped the file size from ~4gb to 200mb.

GadgetAngel, 2021-11-03:
> Thank you so much! I really appreciate it! Not sure if you're aware but the Octopus image is killing your file size. I'm converting the PSD to Illustrator just because thats what I mainly use. Deleting just that one image dropped the file size from ~4gb to 200mb.

Good to know.

I am glad you are able to reuse what I did.

I hope you make your Adobe Illustrator file available to me and others.  When you get done developing your version of the wiring harness, can you please send me a link to your Adobe Illustrator file on you google drive so that I can add it to my github repository?

I really think it is a good practice that every one make up a wiring diagram for their Voron build.

At the present time, I am 3D modeling my whole Voron 2.4 build in Fusion 360.  I want to ensure that all the MODS I am implementing will work on the printer before I start the build process.  I will be making my Fusion 360 model available at a later date.

By 3D modeling (Fusion 360) my whole 3D printer, I will always have a model to refer back to at a later time.

Have fun!

zcohenld, 2021-11-03:
Yeah, absolutely I'll post it! It will take be a bit as I have a lot coming up with work, but when I get it done I will definitely post it.

My wife just okayed me building a Voron this past weekend, so I'm still very much in the early stages of it, but I plan on posting everything I do as well.

I'm building mine in Fusion as well. I have a couple of custom designs I'm thinking of so I want to make sure everything works too. Fusion also integrates with Autodesk Eagle and has its own powerful wiring tool. I'm doing some custom circuit boards in my design so I plan on using Fusion for my circuit layout as well.

GadgetAngel, 2021-11-04:
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

It sounds like you have more experience than I do.  I hope we can work together.  What size of Voron 2.4 are you building?

zcohenld, 2021-11-09:
I'm building 300mm³. Its replacing a CR-10 that is heavily modded so I'm largely keeping the sizes the same.
More than happy to work together on the project! Between work and my family my build is going to be pretty slow, but happy to contribute in any way that I can. I'm going to start the Illustrator file this week at some point.

GadgetAngel, 2021-11-09:
> I'm building 300mm³. Its replacing a CR-10 that is heavily modded so I'm largely keeping the sizes the same. More than happy to work together on the project! Between work and my family my build is going to be pretty slow, but happy to contribute in any way that I can. I'm going to start the Illustrator file this week at some point.

I am building the 250mm³.

I would love for you to look at my design of the litter box, to see if you have any suggestions about it.

Let's use this conversation as a way to share ideas about our Voron builds.

I am still working on the litter box mod. I have been working on it for a month now.  Give me a couple more days and I will post a fusion 360 file of my Voron 2.4 build here so you can talk a look at the litter box mod.

BTW, I looked and EAGLE premium comes with my Fusion 360 subscription.  I have never used EAGLE before but I will try to use the schematic drawing section for my wiring diagram.  Thanks for the tip.

zcohenld, 2021-11-10:
More than happy to look at your design! Just let me know when you push it out.
Eagle is really for custom PCBs, not so much schematics. I thought it could be for that, but it seems its a bit hard for that. I'm looking at other programs since it would be easier than anything else.
I'm ordering most of the materials for my printer tomorrow during Aliexpress's 11/11 sale. It will probably take me three to four months to build it just because of work/family/other obligations. I plan on doing very few mods in the beginning since I cant print in ABS until I get the printer running. Also I like starting from stock and modifying afterwards. Limited mods, or ones I've seen others do well I'm all for implementing from the beginning though.

zcohenld, 2021-12-09:
Hey so I managed to resize the Photoshop file enough to be able to import it into Illustrator. I haven't really done anything to the Illustrator file yet, but thought I'd still share it with you. You can access it [HERE](https://drive.google.com/file/d/1UhOujPA6anQ5diXwj7rjIgV5Nwe1pTmv/view?usp=sharing).

GadgetAngel, 2021-12-15:
> Hey so I managed to resize the Photoshop file enough to be able to import it into Illustrator. I haven't really done anything to the Illustrator file yet, but thought I'd still share it with you. You can access it [HERE](https://drive.google.com/file/d/1UhOujPA6anQ5diXwj7rjIgV5Nwe1pTmv/view?usp=sharing).

You can find my 3D model of my build at https://github.com/GadgetAngel/Voron2.4_My_Build_Log/tree/main/Electronics_Case_Wiring_Diagram/CAD/QUEEN_FUSION360_Files

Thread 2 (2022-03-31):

Voron 2.4r2 side skirts

Quickuser75, 2022-03-31:
HI I AM WONDERING IS YOU HAVE THE SIDE PANEL FOR THE KEWEISI METER
FOR THE VORON 2.4R2 SIDE SKIRTS AS THERE ARE NOT THE SAME AS THE
r2

GadgetAngel, 2022-03-31:
> HI I AM WONDERING IS YOU HAVE THE SIDE PANEL FOR THE KEWEISI METER FOR THE VORON 2.4R2 SIDE SKIRTS AS THERE ARE NOT THE SAME AS THE r2

I intend to update those panels and my whole model to the Voron2.4r2 when I have the time.  It will be about a month before I can get to it.  I need to build my LDO Voron 2.4 kit first and set that printer up so I can start printing the models for my QUEEN build.  Once I have my LDO Voron 2.4 up and running I will update the model for QUEEN and that is when all the fusion360 modeling will be redone to get the skirts adjusted.

Presently, I have to delay the build for my LDO kit because I am working on the Voron DOC sites documentation.  I have 17 pull requests in right now and I have another 14 yet to do.

Please, be patient with me.  Like I said in my Voron Build LOG this is a work in progress.

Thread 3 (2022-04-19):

[FR] Sizings

viappidu, 2022-04-19:
Not a bug, not a feature request anyhow.
I do understand very well it's a work in progress though I cannot understand how you sized/scaled your model.
Is it for shrinkage or any other reason?

In particular, I printed out the "L_SPACER_Bracket_4mm_x1.stl" *and they work fine*, but now that I am making some mods myself I cannot understand your way.

(Thanks in advance)

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

GadgetAngel, 2022-04-20:
>

Yes, it was designed with shrinkage in mind.

I took the DIN bracket outline from the Voron Design Team's own Trident's DIN Bracket for the Voron2.4r2 and copied it onto the "L_SPACER_Bracket_4mm_x1.stl".

The mounting holes size I got from looking at other Voron Design Team parts and I know that ABS will shrink and I looked at what bolt and screw the Voron Design Team used for a parts and that told me what size I should make the hole for the screw head and and what size of hole to use for the screw's shaft. I also rely on fusion 360 software for clearance sizes for screws. See below.

In side Fusion 360 when you select "Surface -> Create -> Hole" and when you select "Clearance" for "Hole Tap Type" the fusion 360 SW will display a pop up menu which contains the following items: "Standard", "Fastener Type", "Size", "Fit".  I use the Standard "Ansi Metric M Profile" which will take into account shrinkage for ABS parts.

The following is what I use
the values are what Fusion 360 produces for:
 Holes: Hole Type: "Counterbore",
 Hole Tap Type: "Clearance",
Drill Point: Flat,
Extents: "Distance".

Standard: "Ansi Metric M Profile",
Fastener Type: "Socket Head Cap Screw",
Fit: "Normal"

Size: M3
     Bolt Hole: 3.4
     Head Diameter: 6.5
     Depth of Head: 3.0

Size: M5
   Bolt Hole: 5.5
   Head Diameter: 10
   Depth of Head: 5

Size: M2
   Bolt Hole: 2.4
   Head Diameter: 4.4
  Depth of Head: 2.0

Size: M2.5
   Bolt Hole: 2.9
   Head Diameter: 5.5
   Depth of Head: 2.5

Torx Rounded Hex Head:
    Bolt Hole: 1.9
    Head Diameter: 4.0
    Depth of Head: 2

There are many sources on how to tap a hole in fusion 360: https://www.seniorcare2share.com/how-to-model-screw-holes-for-3d-printing-supports/

As far as the design of the L bracket DIN support, I stole the hole out line from the Trident's "DIN_frame_mount_x4.stl" part located at https://github.com/VoronDesign/Voron-Trident/blob/main/STLs/ElectronicsBay/DIN_frame_mount_x4.stl

I just imported the model for the Trident into fusion 360 and found the DIN_frame_mount.stl part and then created a sketch of the DIN outline from the original part.  Then copied the sketch over to the part I designed.  So I am relying on the Voron Design Team for the DIN hole clearances.

I hope this answers you question.

BTW, I am like you.  I am just starting to design parts and I am learning as I go.  I hope this helped.

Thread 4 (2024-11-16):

[BUG] Broken images, PDFs, etc

DrFate09, 2024-11-16:
@GadgetAngel wanted to bring to your attention that several assets in your repository are now corrupt, with many being only 1KB in size. For example, most of the assets here are corrupt, https://github.com/GadgetAngel/Voron2.4_My_Build_Log/tree/main/Wiring_Harness_Diagram

Are you able to fix these issues or provide a Google Drive link to your repository assets that you mentioned in your README?

Thanks!

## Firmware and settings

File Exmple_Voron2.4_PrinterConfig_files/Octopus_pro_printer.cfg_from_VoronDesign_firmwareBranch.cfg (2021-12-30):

# This file contains common pin mappings for the BigTreeTech Octopus V1.
# To use this config, the firmware should be compiled for the STM32F446 with a "32KiB bootloader"
# Enable "extra low-level configuration options" and select the "12MHz crystal" as clock reference

# after running "make", copy the generated "klipper/out/klipper.bin" file to a
# file named "firmware.bin" on an SD card and then restart the OctoPus with that SD card.

# See docs/Config_Reference.md for a description of parameters.

## Voron Design Trident 250/300/350mm BigTreeTech OctoPus V1 TMC2209 UART config

## *** THINGS TO CHANGE/CHECK: ***
## MCU paths                            [mcu] section
## Thermistor types                     [extruder] and [heater_bed] sections
## Leadscrew Rotation Distance          [stepper_z], [stepper_z1], [stepper_z2]
## Z Endstop Switch location            [safe_z_home] section
## Z Endstop Switch  offset for Z0      [stepper_z] section
## PID tune                             [extruder] and [heater_bed] sections
## Probe pin                            [probe] section
## Fine tune E steps    

## Thermistor Types
##   "EPCOS 100K B57560G104F"
##   "ATC Semitec 104GT-2"
##   "NTC 100K beta 3950"
##   "Honeywell 100K 135-104LAG-J01"
##   "NTC 100K MGB18-104F39050L32"
##   "AD595"
##   "PT100 INA826"
##===================================================================.

[include mainsail.cfg]
#[include flexplate.cfg]

[save_variables]
filename: /home/pi/klipper_config/.variables.stb

[virtual_sdcard]
path: ~/gcode_files

[pause_resume]
[display_status]

[mcu]
###Change to device found by "ls -l /dev/serial/by-id/" with just one this MCU connected to Pi
serial: /dev/serial/by-id/usb-Klipper_stm32f446xx_49005A000F51383438343939-if00

[printer]
kinematics: corexy
max_velocity: 300
max_accel: 5000
max_z_velocity: 5 #30
max_z_accel: 50 #350
square_corner_velocity: 5.0  

[bed_mesh]
speed: 75
mesh_min: 15, 25
mesh_max: 232, 230
probe_count: 3,3
mesh_pps: 2,2
algorithm: bicubic
bicubic_tension: .05

[mcu rpi]
serial: /tmp/klipper_host_mcu

#[adxl345]
#cs_pin: rpi:None

#[resonance_tester]
#accel_chip: adxl345
##accel_per_hz: 100  # default is 75
#probe_points:
#    125,125,20  # an example

[adxl345]
cs_pin: rpi:None

[resonance_tester]
accel_chip: adxl345
#accel_per_hz: 100  # default is 75
probe_points:


#####################################################################
# 	X/Y Stepper Settings
#####################################################################\

##  B Stepper - Left
##  Connected to MOTOR_0
##  Endstop connected to DIAG_0
[stepper_x]
step_pin: PF13
dir_pin: PF12
enable_pin: !PF14
microsteps: 16
rotation_distance: 40
#full_steps_per_rotation: 400
endstop_pin: PG6
position_min: 0

position_endstop: 250
position_max: 250

homing_speed: 10 #Max 100
homing_retract_dist: 5
homing_positive_dir: true

[tmc2209 stepper_x]
uart_pin: PC4
run_current: 0.900
hold_current: 0.750
#sense_resistor: 0.110 #not sure if needed
stealthchop_threshold: 250


##  A Stepper - Right
##  Connected to MOTOR_1
##  Endstop connected to DIAG_1
[stepper_y]
step_pin: PG0
dir_pin: PG1
enable_pin: !PF15
microsteps: 16
rotation_distance: 40
#full_steps_per_rotation: 400
endstop_pin: PG9
position_endstop: 258
position_max: 258
homing_speed: 10  #Max 100
homing_retract_dist: 5
homing_positive_dir: true

[tmc2209 stepper_y]
uart_pin: PD11
run_current: 0.900
hold_current: 0.750
#sense_resistor: 0.110
stealthchop_threshold: 250


#####################################################################
# 	Z Stepper Settings
#####################################################################

##  Z0 Stepper - Front Left (M1)
##  Connected to MOTOR_2
##  Endstop connected to DIAG_2
[stepper_z]
step_pin: PF11
dir_pin: !PG3
enable_pin: !PG5
microsteps: 16
##T8x4 Lead Screws.  One rotation moves the bed 4mm 
##Change according to integrated steppers purchased
rotation_distance: 8
#full_steps_per_rotation: 200
endstop_pin: PG10
#  Z-position of nozzle (in mm) to z-endstop trigger point relative to print surface (Z0)
#  (+) value = endstop above Z0, (-) value = endstop below
#  Increasing position_endstop brings nozzle closer to the bed
#  After you run Z_ENDSTOP_CALIBRATE, position_endstop will be stored at the very end of your config
#position_endstop: -0.5
## All builds use same Max Z
position_max: 250
position_max: 250
position_min: -2.5
homing_speed: 20

[tmc2209 stepper_z]
uart_pin: PC6
interpolate: False
run_current: 0.650
hold_current: 0.450
#sense_resistor: 0.110
stealthchop_threshold: 30 # old was 30

##  Z1 Stepper - Rear Center (M2)
##  Connected to MOTOR_3
[stepper_z1]
step_pin: PG4
dir_pin: !PC1
enable_pin: !PA0
microsteps: 16
rotation_distance: 8
#full_steps_per_rotation: 200

[tmc2209 stepper_z1]
uart_pin: PC7
interpolate: False
run_current: 0.650
hold_current: 0.450
#sense_resistor: 0.110
stealthchop_threshold: 30 # old was 30

##  Z2 Stepper - Front Right (M3)
##  Connected to MOTOR_4
[stepper_z2]
step_pin: PF9
dir_pin: !PF10
enable_pin: !PG2
microsteps: 16
rotation_distance: 8
#full_steps_per_rotation: 200

[tmc2209 stepper_z2]
uart_pin: PF2
interpolate: False
run_current: 0.650
hold_current: 0.450
#sense_resistor: 0.110
stealthchop_threshold: 30 # old was 30



#####################################################################
#   Extruder
#####################################################################

#   Connected to MOTOR_6
#   Heater - HE0
#   Thermistor - T0
[extruder]
step_pin: PE2
dir_pin: PE3
enable_pin: !PD4
max_extrude_cross_section: 50
max_extrude_only_distance: 700.00
microsteps: 16
# Tune per individual printer
# Default for Bondtech 5mm Bore Drive Gears
#rotation_distance: 22.6789511
#gear_ratio: 50:17
## Bondtech LGX
rotation_distance:  54.45 #55 #for LGX        #for mini AB  21.855 #21.8553543599825 #21.8851878115 #22.6789511 #22.23        # See calibrating rotation_distance on extruders doc
gear_ratio: 45:14, 37:17 #for LGX      # For Mini Afterburner 50:10 
#end LGX
#full_steps_per_rotation: 200
nozzle_diameter: 0.400
filament_diameter: 1.750
pressure_advance: 0.67
pressure_advance_smooth_time: 0.040
heater_pin: PA2
##	Validate the following thermistor type to make sure it is correct
sensor_type: Generic 3950
sensor_pin: PF4
min_extrude_temp: 0
min_temp: 0
max_temp: 300
#control = pid
#pid_kp = 26.213
#pid_ki = 1.304
#pid_kd = 131.721
#Set appropriate once tuning your printer
#pressure_advance: .05
##	Default is 0.040, leave stock
pressure_advance_smooth_time: 0.040

[tmc2209 extruder]
uart_pin: PE1
run_current: 0.5
hold_current: 0.4
#sense_resistor: 0.110
stealthchop_threshold: 30

#####################################################################
# 	Bed Heater
#####################################################################   
[heater_bed]
heater_pin: PA1
##  Choose the correct thermistor for your heater
sensor_type: EPCOS 100K B57560G104F
sensor_pin: PF3
##	Adjust Max Power so your heater doesn't warp your bed
max_power: 1
min_temp: 0
max_temp: 120
control: pid
pid_kp: 58.437
pid_ki: 2.347
pid_kd: 363.769

#####################################################################
# 	Probe
#####################################################################
[probe]
##  Inductive Probe
##  This probe is not used for Z height, only Quad Gantry Leveling

# Select the probe port by type:
## For the PROBE port. Will not work with Diode. May need pull-up resistor from signal to 24V.
# pin: ~!PB7
## For the DIAG_7 port. NEEDS BAT85 DIODE! Change to !PG15 if probe is NO.
pin: PG15
## For Octopus Pro Probe port; NPN and PNP proximity switch types can be set by jumper
# pin: ^PC5

x_offset: 0
y_offset: 22.5
z_offset: 0
speed: 30.0 #20.0
samples: 1
samples_result: average
sample_retract_dist: 2.0
samples_tolerance: 0.05
samples_tolerance_retries: 3

#####################################################################
# 	Fan Control
#####################################################################

##  Print Cooling Fan - FAN0
[fan]
pin: PA8
max_power: 1.0
kick_start_time: 0.5

##  Hotend Fan - FAN1
[heater_fan hotend_fan]
pin: PE5
max_power: 1.0
kick_start_time: 0.5
heater: extruder
heater_temp: 50.0
##  If you are experiencing back flow, you can reduce fan_speed
#fan_speed: 1.0

#[controller_fan controller_fan]
##  Controller fan - FAN2
#pin: PD12
#kick_start_time: 0.5
#heater: heater_bed

#[heater_fan exhaust_fan]
##  Exhaust fan - FAN3
#pin: PD13
#max_power: 1.0
#shutdown_speed: 0.0
#kick_start_time: 5.0
#heater: heater_bed
#heater_temp: 60
#fan_speed: 1.0

#####################################################################
#   LED Control
#####################################################################

#[output_pin caselight]
# Chamber Lighting - HE2 Connector (Optional)
#pin: PB10
#pwm:true
#shutdown_value: 0
#value:1
#cycle_time: 0.01
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

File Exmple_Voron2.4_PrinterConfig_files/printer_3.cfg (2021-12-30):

# This file contains common pin mappings for the Fysetc Spider board.
# To use this config, the firmware should be compiled for the STM32F446.
# When calling "menuconfig", enable "extra low-level configuration setup"
# and select the "12MHz crystal" as clock reference
# For flashing, write the compiled klipper.bin to memory location 0x08000000

# See docs/Config_Reference.md for a description of parameters.

## Voron Design VORON2 250/300/350mm Spider TMC2209 UART config

## *** THINGS TO CHANGE/CHECK: ***
## MCU paths					[mcu] section
## Thermistor types				[extruder] and [heater_bed] sections - See 'sensor types' list at end of file
## Z Endstop Switch location			[safe_z_home] section
## Homing end position				[gcode_macro G32] section
## Z Endstop Switch  offset for Z0		[stepper_z] section
## Probe points					[quad_gantry_level] section
## Min & Max gantry corner postions		[quad_gantry_level] section
## PID tune					[extruder] and [heater_bed] sections
## Fine tune E steps				[extruder] section

# For klicky probe and klipper z calibration
#[include klicky-probe.cfg]
#[include z_calibration.cfg]

[mcu]
##  You need to select 'Communication interface' to USB in 'make menuconfig'
##  when you compile Klipper for Spider
##	Obtain definition by "ls -l /dev/serial/by-id/" then unplug to verify
##--------------------------------------------------------------------
#serial: /dev/serial/by-id/usb-Klipper_stm32f446xx_230032000851363131363530-if00
##	If you want to use the Raspberry uart0 to communicate with Spider, 
##  you need to select 'Communication interface' to 'Serial (on USART1 PA10/PA9)' 
##  in 'make menuconfig' when you compile klipper and set the serial as below
##--------------------------------------------------------------------
serial: /dev/serial/by-id/usb-Klipper_stm32f446xx_2A005A001051383039343538-if00
##--------------------------------------------------------------------

## Uncomment below if you're using the Raspberry uart0 to communicate with Spider
#restart_method: command

[printer]
kinematics: corexy
max_velocity: 300  
max_accel: 3000			        #Max 4000
max_z_velocity: 15			#Max 15 for 12V TMC Drivers, can increase for 24V
max_z_accel: 350
square_corner_velocity: 5.0

#####################################################################
#      X/Y Stepper Settings
#####################################################################

[stepper_x]
##	Connected to X-MOT (B Motor)
step_pin: PE11
dir_pin: PE10
enable_pin: !PE9
rotation_distance: 40
microsteps: 16
full_steps_per_rotation:200  #set to 400 for 0.9 degree stepper
endstop_pin: ^PA1 # X-MAX
position_min: 0

##--------------------------------------------------------------------

##	Uncomment below for 250mm build
#position_endstop: 250
#position_max: 250

##	Uncomment for 300mm build
#position_endstop: 300
#position_max: 300

##	Uncomment for 350mm build
position_endstop: 350
position_max: 350

##--------------------------------------------------------------------
homing_speed: 25   #Max 100
homing_retract_dist: 5
homing_positive_dir: true

#    Make sure to update below for your relevant driver (2208 or 2209)
[tmc2209 stepper_x]
uart_pin: PE7
interpolate: True
run_current: 1.0
hold_current: 0.8
sense_resistor: 0.110
stealthchop_threshold: 0

#    Make sure to update below for your relevant driver (5160)
#[tmc5160 stepper_x] 
#spi_bus: spi4 
#cs_pin: PE7 
#interpolate: True
#diag1_pin: PB14 
#run_current: 0.800 
#hold_current: 0.500
##stealthchop_threshold: 0

[stepper_y]
##	Connected to Y-MOT (A Motor)
step_pin: PD8
dir_pin: PB12
enable_pin: !PD9
rotation_distance: 40
microsteps: 16
full_steps_per_rotation:200  #set to 400 for 0.9 degree stepper
endstop_pin: ^PA2 # Y-MAX
position_min: 0
##--------------------------------------------------------------------

##	Uncomment for 250mm build
#position_endstop: 250
#position_max: 250

##	Uncomment for 300mm build
#position_endstop: 300
#position_max: 300

##	Uncomment for 350mm build
position_endstop: 350
position_max: 350

##--------------------------------------------------------------------
homing_speed: 25  #Max 100
homing_retract_dist: 5
homing_positive_dir: true

#	Make sure to update below for your relevant driver (2208 or 2209)
[tmc2209 stepper_y]
uart_pin: PE15
interpolate: True
run_current: 1.0
hold_current: 0.8
sense_resistor: 0.110
stealthchop_threshold: 0

#       Make sure to update below for your relevant driver (5160)
#[tmc5160 stepper_y] 
#spi_bus: spi4 
#cs_pin: PE15
##diag1_pin: PB13
#interpolate: True 
#run_current: 0.8
#hold_current: 0.7
##stealthchop_threshold: 0

## In E3-MOT Position
## Z0 Stepper - Z Left Motor
[stepper_z]
step_pin: PD12
dir_pin: !PC4
enable_pin: !PE8
##T8x4 Lead Screws.  One rotation moves the bed 4mm 
##Change according to integrated steppers purchased
rotation_distance: 4
full_steps_per_rotation: 200
microsteps: 16
##  In Z- Position
endstop_pin: ^PA0
##  Z-position of nozzle (in mm) to z-endstop trigger point relative to print surface (Z0)
##  (+) value = endstop above Z0, (-) value = endstop below
##	Increasing position_endstop brings nozzle closer to the bed
##  After you run Z_ENDSTOP_CALIBRATE, position_endstop will be stored at the very end of your config
#position_endstop: -0.5
## All builds use same Max Z
position_max: 125

##--------------------------------------------------------------------
position_min: -10
homing_speed: 8
second_homing_speed: 3
homing_retract_dist: 5

##	Make sure to update below for your relevant driver (2208 or 2209)
[tmc2209 stepper_z]
uart_pin: PA15
uart_address: 0
interpolate: True
run_current: 1.2
hold_current: 1.0
sense_resistor: 0.110
stealthchop_threshold: 0

##	In E2-MOT Position
##	Z1 Stepper - Z Rear Motor
[stepper_z1]
step_pin: PE2
dir_pin: !PE4
enable_pin: !PE3
rotation_distance: 4
full_steps_per_rotation: 200
microsteps: 16

##	Make sure to update below for your relevant driver (2208 or 2209)
[tmc2209 stepper_z1]
uart_pin: PC14
interpolate: True
run_current: 1.2
hold_current: 1.0
sense_resistor: 0.110
stealthchop_threshold: 0

##	In E1-MOT Position
##	Z2 Stepper - Z Right Motor
[stepper_z2]
step_pin: PE6
dir_pin: !PC13
enable_pin: !PE5
rotation_distance: 4
full_steps_per_rotation: 200
microsteps: 16

##	Make sure to update below for your relevant driver (2208 or 2209)
[tmc2209 stepper_z2]
uart_pin: PC15
interpolate: true
run_current: 1.2
hold_current: 1.0
sense_resistor: 0.110
stealthchop_threshold: 0

#####################################################################
#   Extruder
#####################################################################

##	In E0-MOT Position
[extruder]
step_pin: PD5
dir_pin: PD6
enable_pin: !PD4

##	Update value below when you perform extruder calibration
##	If you ask for 100mm of filament, but in reality it is 98mm:
##	rotation_distance = <previous_rotation_distance> * <actual_extrude_distance> / 100
##  22.6789511 is a good starting point
rotation_distance: 22.6789511	#Bondtech 5mm Drive Gears
##	Update Gear Ratio depending on your Extruder Type
##	Use 50:17 for Afterburner/Clockwork (BMG Gear Ratio)
##	Use 80:20 for M4, M3.1
gear_ratio: 50:17				#BMG Gear Ratio
microsteps: 16
full_steps_per_rotation: 200	#200 for 1.8 degree, 400 for 0.9 degree
nozzle_diameter: 0.400
filament_diameter: 1.75
##      In E0 OUT Position
heater_pin: PB15
##	Validate the following thermistor type to make sure it is correct
sensor_type: ATC Semitec 104GT-2
sensor_pin: PC0
min_temp: -100
max_temp: 270
max_power: 1.0
min_extrude_temp: 170
control = pid
pid_kp = 26.213
pid_ki = 1.304
pid_kd = 131.721
##	Try to keep pressure_advance below 1.0
pressure_advance: 0.05
##	Default is 0.040, leave stock
pressure_advance_smooth_time: 0.040

##	In E0-MOT Position
##	Make sure to update below for your relevant driver (2208 or 2209)
[tmc2209 extruder]
uart_pin: PD7
interpolate: false
run_current: 0.5
hold_current: 0.3
sense_resistor: 0.110
stealthchop_threshold: 0

#####################################################################
#   Bed Heater
#####################################################################
[heater_bed]
##	SSR Pin - In BED OUT position
heater_pin: PB4
sensor_type: NTC 100K MGB18-104F39050L32
#sensor_pin: PC3 # Spider v1.x
sensor_pin: PB0 # Spider v2.x
##	Adjust Max Power so your heater doesn't warp your bed
max_power: 0.6
min_temp: -100
max_temp: 120
control: pid
pid_kp: 58.437
pid_ki: 2.347
pid_kd: 363.769

#####################################################################
#	Probe
#####################################################################

[probe]
#	Inductive Probe - If you use this section , please comment the [bltouch] section
#	This probe is not used for Z height, only Quad Gantry Leveling
#	In Z+ position
#	If your probe is NO instead of NC, add change pin to ^PA3
pin: ^PA3
x_offset: 0
y_offset: 25.0
z_offset: 0
speed: 10.0
samples: 3
samples_result: median
sample_retract_dist: 5.0
samples_tolerance: 0.01 #0.006
samples_tolerance_retries: 3
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

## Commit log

2021-10-17 Added information on Motor Torque Curves
2021-10-17 Added Note about V3.rabbit Toolhead board
2021-10-17 Update Wiring Harness Diagram
2021-10-17 update Wire_Harness_Diagram
2021-10-17 Add Spider V1.1 wiring diagram to Resources
2021-10-18 update Octopus Pro original PIN diagram
2021-11-02 Adding Adobe Photoshop file for Wiring Harness
2021-12-13 Added 3D model for QUEEN Build
    [QUEEN_Voron_2.4_Build v89.f3d]
2021-12-13 Add CAD file for Litter Box Mod
    [QUEEN_Voron_2.4_Build v89.f3d]
2021-12-13 Add STEP files
    [60mm_Shaft_Jig.stl, 60mm_Shaft_Jig_v2.step, AB_pulley_jig.stl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]
2021-12-13 Update STEP files
    [QUEEN_Voron_2.4_Build_v89.step]
2021-12-14 Update CAD files
    [Electronics_SubAssembly_from_QUEEN_Voron_2.4_Build_v98.f3d, Litter_Box_MOD_SubAssembly_from_QUEEN_Voron_2.4_Build_v98.f3d, My_Litter_Box_MOD_Electronics_only_f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]
2021-12-14 Add CAD files
    [BTT_piTFT_articulating_arm_from_QUEEN_Voron_2.4_Build_v98.f3d, Bottom_Electroics_Case_from_QUEEN_Voron_2.4_Build_v98.f3d, Electronics_SubAssembly_from_QUEEN_Vo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]
2021-12-16 Add mods to .stl files
    [GadgetAngel's_Cover_Magnetic_Normal.stl, GadgetAngel_Front_Idler_Mag_Cover.stl]
2021-12-20 Add .stl files list for Build and MODs
    [1_Channel_Solid_State_Relay_Horizontal_Fixed_Mount_x1.stl, 1_Channel_Solid_State_Relay_Horizontal_Slider_Interface_x1.stl, 1_Channel_Solid_State_Relay_Horizont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]
2021-12-22 Update CAD files and .stl files
    [BTT_piTFT_articulating_arm_from_QUEEN_Voron_2.4_Build_v98.f3d, Bottom_Electroics_Case_from_QUEEN_Voron_2.4_Build_v98.f3d, CableClip_x20.3mf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]
2021-12-22 Update .stl files
    [GA_brush_holder_sheet_stop_Spacer_15.697mm_x1.stl, QUEEN_Printed_Part_Reference.xlsx, Z-Joint_0,08_x6.3mf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]
2021-12-22 Update Excel Spreadsheet for .stl list
    [QUEEN_Printed_Part_Reference.xlsx]
2021-12-22 Update EXCEL spreadsheet of .STL parts list
    [QUEEN_Printed_Part_Reference.xlsx]
2021-12-22 Update EXCEL spreadsheet
    [QUEEN_Printed_Part_Reference.xlsx]
2021-12-22 Update CAD files to include Euclide Probe option
    [QUEEN_Printed_Part_Reference.xlsx, QUEEN_Voron_2.4_Build.f3d, QUEENv98_SubAssb_Gantry.f3d]
2021-12-22 Added Euclid Probe files to EXCEL spreadsheet
    [Derpimus_OmronFotek90_Main_x1.stl, Derpimus_Voron2.4OmronRotatedXRailDock_x1.stl, QUEEN_Printed_Part_Reference.xlsx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]
2021-12-22 Update files
    [LitterBox_Stationary_Bar_x1.stl, Litterbox_Voron2.4_pcb_din_clip_using_selftapping_screw_x1.stl, Octopus_bracket_2pc.stl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]
2021-12-24 Add Voron Design Parts Logo for Trident
    [QUEEN_Printed_Part_Reference.xlsx, Voron-Trident_DesignLogov51.f3d, Voron2.4DesignLogov34.f3d]
2021-12-24 include .STL files for Voron-Trident_Design_Logo
    [Voron-Trident_DesignLogo.stl, Voron-Trident_DesignLogo_Dimensions_X_216.51_Y_250.00_Z_1.75.stl, Voron-Trident_DesignLogo_Dimensions_X_259.80_Y_300.00_Z_2.10.st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]
2021-12-24 Include .STL files for Voron-Trident and .SVG
    [250_deck.dxf, 250_rear.dxf, 300_deck.dxf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]
2021-12-30 Updated ZIP files
    [Voron-Trident_DesignLogo_v56.f3d, Voron2.4DesignLogov34.f3d]
2021-12-31 Updated .stl files
    [5015-deearing-tool-b_x1.stl, 5015-deearing-tool_x1.stl, AB-BN-28_Hotend-Dragon-Back_x1.stl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]
2021-12-31 Update .STL files being used
    [AB_mount_magnet_holder_x2.stl, AB_mount_magnet_press_x2.stl, AB_mount_press_Helper_x2.stl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]
2021-12-31 Update EXCEL .STL files list
    [QUEEN_Printed_Part_Reference.xlsx]
2022-01-05 Update .stl file and add resources
    [RD-50A-Horizontal_Mount_x1.stl, RD-50A_PSU_SideBracket-Interface_x1.stl, RD-50A_Vertical_Mount_x1.stl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]
2022-01-06 Update README for AC Wiring Diagram
2022-01-06 Update AC Electrical Wiring Diagram
2022-01-07 AC Electrical Wiring to for a common V- for PSUs
    [Enraged Rabbit Project - Sourcing Guide.xlsx, LGX Front Mount_fromERCFproj_x1.stl, Skirts JST-SM - 4-Pinx2 Rabbit Hole_x1.stl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]
2022-01-07 New Version 2.0 of Voron 2.4 AC Wiring Diagram
2022-01-08 Add 3D CAD file MandalaRoseWorks MIC6 Build Plate
2022-01-08 Update Stealthburner .STL files
    [Stealthburner_toolhead_rapido_front_beta0_x1.stl, [a]_stealthburner_main_body_beta2_x1.stl, [a]_stealthburner_main_body_beta3_x1.stl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]
2022-01-10 Update Resource files
    [Just_LED_Section (1).stl, LGX Front Mount_fromERCFproj_x1.stl, LGX_on_AfterBurner_Adapter_ERCF_Sensor_fromERCFproj.stl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]
2022-01-11 Add BIG RED button calc for Amps
2022-01-15 Update AC Wiring Diagram
2022-01-17 Create Panduit PanelMax Din Wire Ducts.pdf
2022-01-17 Update .STL files and Resources
    [StealthburnerCW1Body.stl, StealthburnerCW1PCBCover.stl]
2022-01-19 Add tools for Linear Rails
    [Middle.stl, Sides_x2.stl, Tapa_MGN12.STL]
2022-01-21 update Resources
    [stealthburner_TOOL_led_soldering_stand_v1.stl]
2022-01-29 Update Resources for Spider V2.2 board
